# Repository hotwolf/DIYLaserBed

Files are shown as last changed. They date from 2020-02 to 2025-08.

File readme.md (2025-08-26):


# RevB
This is a DIY laser bed for K40 cutters and clones.
inside

<span></span>

---
## Table of Contents
1. [Parts list](#Parts_list)
1. [DIYLB Top Assembly](#DIYLB_top_assembly)
1. [DIYLB Carriage D Assembly](#DIYLB_carriage_D_assembly)
1. [DIYLB Carriage C Assembly](#DIYLB_carriage_C_assembly)
1. [DIYLB Carriage AB Assembly](#DIYLB_carriage_AB_assembly)
1. [DIYLB Carriage B Assembly](#DIYLB_carriage_B_assembly)
1. [DIYLB Carriage A Assembly](#DIYLB_carriage_A_assembly)
1. [DIYLB Rail Assembly](#DIYLB_rail_assembly)
1. [DIYLB Crank Assembly](#DIYLB_crank_assembly)
1. [DIYLB Idler Assembly](#DIYLB_idler_assembly)
1. [DIYLB Lower Bearing Assembly](#DIYLB_lower_bearing_assembly)
1. [DIYLB Base Right Assembly](#DIYLB_base_right_assembly)
1. [DIYLB Magnet Cover Assembly](#DIYLB_magnet_cover_assembly)
1. [DIYLB Magnet Assembly](#DIYLB_magnet_assembly)
1. [DIYLB Base Center Assembly](#DIYLB_base_center_assembly)
1. [DIYLB Base Left Assembly](#DIYLB_base_left_assembly)
1. [DIYLB Base Assembly](#DIYLB_Base_assembly)
1. [DIYLB Crank To Base Assembly](#DIYLB_crank_to_base_assembly)
1. [DIYLB Columns To Base Assembly](#DIYLB_columns_to_base_assembly)
1. [DIYLB Bed To Columns Assembly](#DIYLB_bed_to_columns_assembly)
1. [DIYLB Beams To Bed Assembly](#DIYLB_beams_to_bed_assembly)
1. [DIYLB Top To Columns Assembly](#DIYLB_top_to_columns_assembly)
1. [DIYLB Belt Assembly](#DIYLB_belt_assembly)

<span></span>
[Top](#TOP)

---

## Parts list
| <span style="writing-mode: vertical-rl; text-orientation: mixed;">2 x DIYLB&nbsp;Top</span> | <span style="writing-mode: vertical-rl; text-orientation: mixed;">DIYLB&nbsp;Carriage&nbsp;D</span> | <span style="writing-mode: vertical-rl; text-orientation: mixed;">DIYLB&nbsp;Carriage&nbsp;C</span> | <span style="writing-mode: vertical-rl; text-orientation: mixed;">2 x DIYLB&nbsp;Carriage&nbsp;AB</span> | <span style="writing-mode: vertical-rl; text-orientation: mixed;">DIYLB&nbsp;Carriage&nbsp;B</span> | <span style="writing-mode: vertical-rl; text-orientation: mixed;">DIYLB&nbsp;Carriage&nbsp;A</span> | <span style="writing-mode: vertical-rl; text-orientation: mixed;">4 x DIYLB&nbsp;Rail</span> | <span style="writing-mode: vertical-rl; text-orientation: mixed;">DIYLB&nbsp;Crank</span> | <span style="writing-mode: vertical-rl; text-orientation: mixed;">DIYLB&nbsp;Idler</span> | <span style="writing-mode: vertical-rl; text-orientation: mixed;">4 x DIYLB&nbsp;Lower&nbsp;Bearing</span> | <span style="writing-mode: vertical-rl; text-orientation: mixed;">DIYLB&nbsp;Base&nbsp;Right</span> | <span style="writing-mode: vertical-rl; text-orientation: mixed;">4 x DIYLB&nbsp;Magnet&nbsp;Cover</span> | <span style="writing-mode: vertical-rl; text-orientation: mixed;">4 x DIYLB&nbsp;Magnet</span> | <span style="writing-mode: vertical-rl; text-orientation: mixed;">2 x DIYLB&nbsp;Base&nbsp;Center</span> | <span style="writing-mode: vertical-rl; text-orientation: mixed;">DIYLB&nbsp;Base&nbsp;Left</span> | <span style="writing-mode: vertical-rl; text-orientation: mixed;">DIYLB&nbsp;Base</span> | <span style="writing-mode: vertical-rl; text-orientation: mixed;">DIYLB&nbsp;Crank&nbsp;To&nbsp;Base</span> | <span style="writing-mode: vertical-rl; text-orientation: mixed;">DIYLB&nbsp;Columns&nbsp;To&nbsp;Base</span> | <span style="writing-mode: vertical-rl; text-orientation: mixed;">DIYLB&nbsp;Bed&nbsp;To&nbsp;Columns</span> | <span style="writing-mode: vertical-rl; text-orientation: mixed;">DIYLB&nbsp;Beams&nbsp;To&nbsp;Bed</span> | <span style="writing-mode: vertical-rl; text-orientation: mixed;">DIYLB&nbsp;Top&nbsp;To&nbsp;Columns</span> | <span style="writing-mode: vertical-rl; text-orientation: mixed;">DIYLB&nbsp;Belt</span> | <span style="writing-mode: vertical-rl; text-orientation: mixed;">TOTALS</span> |  |
|---:|---:|---:|---:|---:|---:|---:|---:|---:|---:|---:|---:|---:|---:|---:|---:|---:|---:|---:|---:|---:|---:|---:|:---|
|  |  |  |  |  |  |  |  |  |  |  |  |  |  |  |  |  |  |  |  |  |  | | **Vitamins** |
| &nbsp;&nbsp;.&nbsp; | &nbsp;&nbsp;.&nbsp; | &nbsp;&nbsp;.&nbsp; | &nbsp;&nbsp;.&nbsp; | &nbsp;&nbsp;.&nbsp; | &nbsp;&nbsp;.&nbsp; | &nbsp;&nbsp;.&nbsp; | &nbsp;&nbsp;2&nbsp; | &nbsp;&nbsp;.&nbsp; | &nbsp;&nbsp;4&nbsp; | &nbsp;&nbsp;.&nbsp; | &nbsp;&nbsp;.&nbsp; | &nbsp;&nbsp;.&nbsp; | &nbsp;&nbsp;.&nbsp; | &nbsp;&nbsp;.&nbsp; | &nbsp;&nbsp;.&nbsp; | &nbsp;&nbsp;.&nbsp; | &nbsp;&nbsp;.&nbsp; | &nbsp;&nbsp;.&nbsp; | &nbsp;&nbsp;.&nbsp; | &nbsp;&nbsp;.&nbsp; | &nbsp;&nbsp;.&nbsp; |  &nbsp;&nbsp;6&nbsp; | &nbsp;&nbsp; Ball bearing 608-2RS 8mm x 22mm x 7mm |
| &nbsp;&nbsp;.&nbsp; | &nbsp;&nbsp;.&nbsp; | &nbsp;&nbsp;.&nbsp; | &nbsp;&nbsp;.&nbsp; | &nbsp;&nbsp;.&nbsp; | &nbsp;&nbsp;.&nbsp; | &nbsp;&nbsp;.&nbsp; | &nbsp;&nbsp;.&nbsp; | &nbsp;&nbsp;.&nbsp; | &nbsp;&nbsp;.&nbsp; | &nbsp;&nbsp;.&nbsp; | &nbsp;&nbsp;.&nbsp; | &nbsp;&nbsp;.&nbsp; | &nbsp;&nbsp;.&nbsp; | &nbsp;&nbsp;.&nbsp; | &nbsp;&nbsp;.&nbsp; | &nbsp;&nbsp;.&nbsp; | &nbsp;&nbsp;.&nbsp; | &nbsp;&nbsp;.&nbsp; | &nbsp;&nbsp;.&nbsp; | &nbsp;&nbsp;.&nbsp; | &nbsp;&nbsp;1&nbsp; |  &nbsp;&nbsp;1&nbsp; | &nbsp;&nbsp; Belt GT2 x 6mm x 1222mm |
| &nbsp;&nbsp;.&nbsp; | &nbsp;&nbsp;.&nbsp; | &nbsp;&nbsp;.&nbsp; | &nbsp;&nbsp;.&nbsp; | &nbsp;&nbsp;.&nbsp; | &nbsp;&nbsp;.&nbsp; | &nbsp;&nbsp;.&nbsp; | &nbsp;&nbsp;.&nbsp; | &nbsp;&nbsp;.&nbsp; | &nbsp;&nbsp;4&nbsp; | &nbsp;&nbsp;.&nbsp; | &nbsp;&nbsp;4&nbsp; | &nbsp;&nbsp;.&nbsp; | &nbsp;&nbsp;.&nbsp; | &nbsp;&nbsp;.&nbsp; | &nbsp;&nbsp;.&nbsp; | &nbsp;&nbsp;.&nbsp; | &nbsp;&nbsp;.&nbsp; | &nbsp;&nbsp;.&nbsp; | &nbsp;&nbsp;.&nbsp; | &nbsp;&nbsp;.&nbsp; | &nbsp;&nbsp;.&nbsp; |  &nbsp;&nbsp;8&nbsp; | &nbsp;&nbsp; Euro-Cent coin |
| &nbsp;&nbsp;.&nbsp; | &nbsp;&nbsp;.&nbsp; | &nbsp;&nbsp;.&nbsp; | &nbsp;&nbsp;2&nbsp; | &nbsp;&nbsp;.&nbsp; | &nbsp;&nbsp;.&nbsp; | &nbsp;&nbsp;.&nbsp; | &nbsp;&nbsp;.&nbsp; | &nbsp;&nbsp;.&nbsp; | &nbsp;&nbsp;.&nbsp; | &nbsp;&nbsp;.&nbsp; | &nbsp;&nbsp;.&nbsp; | &nbsp;&nbsp;.&nbsp; | &nbsp;&nbsp;.&nbsp; | &nbsp;&nbsp;.&nbsp; | &nbsp;&nbsp;.&nbsp; | &nbsp;&nbsp;.&nbsp; | &nbsp;&nbsp;.&nbsp; | &nbsp;&nbsp;.&nbsp; | &nbsp;&nbsp;.&nbsp; | &nbsp;&nbsp;.&nbsp; | &nbsp;&nbsp;.&nbsp; |  &nbsp;&nbsp;2&nbsp; | &nbsp;&nbsp; Extrusion E2020 x 235mm |
| &nbsp;&nbsp;.&nbsp; | &nbsp;&nbsp;.&nbsp; | &nbsp;&nbsp;.&nbsp; | &nbsp;&nbsp;.&nbsp; | &nbsp;&nbsp;.&nbsp; | &nbsp;&nbsp;.&nbsp; | &nbsp;&nbsp;.&nbsp; | &nbsp;&nbsp;.&nbsp; | &nbsp;&nbsp;.&nbsp; | &nbsp;&nbsp;.&nbsp; | &nbsp;&nbsp;1&nbsp; | &nbsp;&nbsp;.&nbsp; | &nbsp;&nbsp;.&nbsp; | &nbsp;&nbsp;.&nbsp; | &nbsp;&nbsp;1&nbsp; | &nbsp;&nbsp;.&nbsp; | &nbsp;&nbsp;.&nbsp; | &nbsp;&nbsp;.&nbsp; | &nbsp;&nbsp;.&nbsp; | &nbsp;&nbsp;.&nbsp; | &nbsp;&nbsp;.&nbsp; | &nbsp;&nbsp;.&nbsp; |  &nbsp;&nbsp;2&nbsp; | &nbsp;&nbsp; Extrusion E2020 x 300mm |
| &nbsp;&nbsp;.&nbsp; | &nbsp;&nbsp;.&nbsp; | &nbsp;&nbsp;.&nbsp; | &nbsp;&nbsp;.&nbsp; | &nbsp;&nbsp;.&nbsp; | &nbsp;&nbsp;.&nbsp; | &nbsp;&nbsp;.&nbsp; | &nbsp;&nbsp;.&nbsp; | &nbsp;&nbsp;.&nbsp; | &nbsp;&nbsp;.&nbsp; | &nbsp;&nbsp;.&nbsp; | &nbsp;&nbsp;.&nbsp; | &nbsp;&nbsp;.&nbsp; | &nbsp;&nbsp;2&nbsp; | &nbsp;&nbsp;.&nbsp; | &nbsp;&nbsp;.&nbsp; | &nbsp;&nbsp;.&nbsp; | &nbsp;&nbsp;.&nbsp; | &nbsp;&nbsp;.&nbsp; | &nbsp;&nbsp;.&nbsp; | &nbsp;&nbsp;.&nbsp; | &nbsp;&nbsp;.&nbsp; |  &nbsp;&nbsp;2&nbsp; | &nbsp;&nbsp; Extrusion E2020 x 320mm |
| &nbsp;&nbsp;.&nbsp; | &nbsp;&nbsp;.&nbsp; | &nbsp;&nbsp;.&nbsp; | &nbsp;&nbsp;.&nbsp; | &nbsp;&nbsp;.&nbsp; | &nbsp;&nbsp;.&nbsp; | &nbsp;&nbsp;4&nbsp; | &nbsp;&nbsp;.&nbsp; | &nbsp;&nbsp;.&nbsp; | &nbsp;&nbsp;.&nbsp; | &nbsp;&nbsp;.&nbsp; | &nbsp;&nbsp;.&nbsp; | &nbsp;&nbsp;.&nbsp; | &nbsp;&nbsp;.&nbsp; | &nbsp;&nbsp;.&nbsp; | &nbsp;&nbsp;.&nbsp; | &nbsp;&nbsp;.&nbsp; | &nbsp;&nbsp;.&nbsp; | &nbsp;&nbsp;.&nbsp; | &nbsp;&nbsp;.&nbsp; | &nbsp;&nbsp;.&nbsp; | &nbsp;&nbsp;.&nbsp; |  &nbsp;&nbsp;4&nbsp; | &nbsp;&nbsp; Extrusion E2020 x 70mm |
| &nbsp;&nbsp;.&nbsp; | &nbsp;&nbsp;.&nbsp; | &nbsp;&nbsp;.&nbsp; | &nbsp;&nbsp;.&nbsp; | &nbsp;&nbsp;.&nbsp; | &nbsp;&nbsp;.&nbsp; | &nbsp;&nbsp;.&nbsp; | &nbsp;&nbsp;1&nbsp; | &nbsp;&nbsp;.&nbsp; | &nbsp;&nbsp;.&nbsp; | &nbsp;&nbsp;.&nbsp; | &nbsp;&nbsp;.&nbsp; | &nbsp;&nbsp;.&nbsp; | &nbsp;&nbsp;.&nbsp; | &nbsp;&nbsp;.&nbsp; | &nbsp;&nbsp;.&nbsp; | &nbsp;&nbsp;.&nbsp; | &nbsp;&nbsp;.&nbsp; | &nbsp;&nbsp;.&nbsp; | &nbsp;&nbsp;.&nbsp; | &nbsp;&nbsp;.&nbsp; | &nbsp;&nbsp;.&nbsp; |  &nbsp;&nbsp;1&nbsp; | &nbsp;&nbsp; Extrusion E2040 x 60mm |
| &nbsp;&nbsp;.&nbsp; | &nbsp;&nbsp;.&nbsp; | &nbsp;&nbsp;.&nbsp; | &nbsp;&nbsp;.&nbsp; | &nbsp;&nbsp;.&nbsp; | &nbsp;&nbsp;.&nbsp; | &nbsp;&nbsp;.&nbsp; | &nbsp;&nbsp;1&nbsp; | &nbsp;&nbsp;.&nbsp; | &nbsp;&nbsp;.&nbsp; | &nbsp;&nbsp;.&nbsp; | &nbsp;&nbsp;.&nbsp; | &nbsp;&nbsp;.&nbsp; | &nbsp;&nbsp;.&nbsp; | &nbsp;&nbsp;.&nbsp; | &nbsp;&nbsp;.&nbsp; | &nbsp;&nbsp;.&nbsp; | &nbsp;&nbsp;.&nbsp; | &nbsp;&nbsp;.&nbsp; | &nbsp;&nbsp;.&nbsp; | &nbsp;&nbsp;.&nbsp; | &nbsp;&nbsp;.&nbsp; |  &nbsp;&nbsp;1&nbsp; | &nbsp;&nbsp; Extrusion E2040 x 70mm |
| &nbsp;&nbsp;.&nbsp; | &nbsp;&nbsp;.&nbsp; | &nbsp;&nbsp;.&nbsp; | &nbsp;&nbsp;.&nbsp; | &nbsp;&nbsp;.&nbsp; | &nbsp;&nbsp;.&nbsp; | &nbsp;&nbsp;.&nbsp; | &nbsp;&nbsp;.&nbsp; | &nbsp;&nbsp;.&nbsp; | &nbsp;&nbsp;.&nbsp; | &nbsp;&nbsp;.&nbsp; | &nbsp;&nbsp;.&nbsp; | &nbsp;&nbsp;.&nbsp; | &nbsp;&nbsp;.&nbsp; | &nbsp;&nbsp;.&nbsp; | &nbsp;&nbsp;.&nbsp; | &nbsp;&nbsp;.&nbsp; | &nbsp;&nbsp;.&nbsp; | &nbsp;&nbsp;.&nbsp; | &nbsp;&nbsp;1&nbsp; | &nbsp;&nbsp;.&nbsp; | &nbsp;&nbsp;.&nbsp; |  &nbsp;&nbsp;1&nbsp; | &nbsp;&nbsp; Flat section 15mmx2mm, 272mm |
| &nbsp;&nbsp;.&nbsp; | &nbsp;&nbsp;.&nbsp; | &nbsp;&nbsp;.&nbsp; | &nbsp;&nbsp;.&nbsp; | &nbsp;&nbsp;.&nbsp; | &nbsp;&nbsp;.&nbsp; | &nbsp;&nbsp;.&nbsp; | &nbsp;&nbsp;.&nbsp; | &nbsp;&nbsp;.&nbsp; | &nbsp;&nbsp;.&nbsp; | &nbsp;&nbsp;.&nbsp; | &nbsp;&nbsp;.&nbsp; | &nbsp;&nbsp;.&nbsp; | &nbsp;&nbsp;.&nbsp; | &nbsp;&nbsp;.&nbsp; | &nbsp;&nbsp;.&nbsp; | &nbsp;&nbsp;.&nbsp; | &nbsp;&nbsp;.&nbsp; | &nbsp;&nbsp;.&nbsp; | &nbsp;&nbsp;4&nbsp; | &nbsp;&nbsp;.&nbsp; | &nbsp;&nbsp;.&nbsp; |  &nbsp;&nbsp;4&nbsp; | &nbsp;&nbsp; Flat section 15mmx2mm, 316mm |
| &nbsp;&nbsp;.&nbsp; | &nbsp;&nbsp;.&nbsp; | &nbsp;&nbsp;.&nbsp; | &nbsp;&nbsp;.&nbsp; | &nbsp;&nbsp;.&nbsp; | &nbsp;&nbsp;.&nbsp; | &nbsp;&nbsp;.&nbsp; | &nbsp;&nbsp;2&nbsp; | &nbsp;&nbsp;.&nbsp; | &nbsp;&nbsp;.&nbsp; | &nbsp;&nbsp;2&nbsp; | &nbsp;&nbsp;.&nbsp; | &nbsp;&nbsp;.&nbsp; | &nbsp;&nbsp;.&nbsp; | &nbsp;&nbsp;4&nbsp; | &nbsp;&nbsp;.&nbsp; | &nbsp;&nbsp;.&nbsp; | &nbsp;&nbsp;.&nbsp; | &nbsp;&nbsp;.&nbsp; | &nbsp;&nbsp;.&nbsp; | &nbsp;&nbsp;.&nbsp; | &nbsp;&nbsp;.&nbsp; |  &nbsp;&nbsp;8&nbsp; | &nbsp;&nbsp; L-Bracket (20x20) |
| &nbsp;&nbsp;.&nbsp; | &nbsp;&nbsp;.&nbsp; | &nbsp;&nbsp;.&nbsp; | &nbsp;&nbsp;.&nbsp; | &nbsp;&nbsp;.&nbsp; | &nbsp;&nbsp;.&nbsp; | &nbsp;&nbsp;4&nbsp; | &nbsp;&nbsp;.&nbsp; | &nbsp;&nbsp;.&nbsp; | &nbsp;&nbsp;.&nbsp; | &nbsp;&nbsp;.&nbsp; | &nbsp;&nbsp;.&nbsp; | &nbsp;&nbsp;.&nbsp; | &nbsp;&nbsp;.&nbsp; | &nbsp;&nbsp;.&nbsp; | &nbsp;&nbsp;.&nbsp; | &nbsp;&nbsp;.&nbsp; | &nbsp;&nbsp;.&nbsp; | &nbsp;&nbsp;.&nbsp; | &nbsp;&nbsp;.&nbsp; | &nbsp;&nbsp;.&nbsp; | &nbsp;&nbsp;.&nbsp; |  &nbsp;&nbsp;4&nbsp; | &nbsp;&nbsp; Linear rail MGN7 x 70mm |
| &nbsp;&nbsp;.&nbsp; | &nbsp;&nbsp;1&nbsp; | &nbsp;&nbsp;1&nbsp; | &nbsp;&nbsp;.&nbsp; | &nbsp;&nbsp;1&nbsp; | &nbsp;&nbsp;1&nbsp; | &nbsp;&nbsp;.&nbsp; | &nbsp;&nbsp;.&nbsp; | &nbsp;&nbsp;.&nbsp; | &nbsp;&nbsp;.&nbsp; | &nbsp;&nbsp;.&nbsp; | &nbsp;&nbsp;.&nbsp; | &nbsp;&nbsp;.&nbsp; | &nbsp;&nbsp;.&nbsp; | &nbsp;&nbsp;.&nbsp; | &nbsp;&nbsp;.&nbsp; | &nbsp;&nbsp;.&nbsp; | &nbsp;&nbsp;.&nbsp; | &nbsp;&nbsp;.&nbsp; | &nbsp;&nbsp;.&nbsp; | &nbsp;&nbsp;.&nbsp; | &nbsp;&nbsp;.&nbsp; |  &nbsp;&nbsp;4&nbsp; | &nbsp;&nbsp; Linear rail carriage MGN7C |
| &nbsp;&nbsp;.&nbsp; | &nbsp;&nbsp;.&nbsp; | &nbsp;&nbsp;.&nbsp; | &nbsp;&nbsp;.&nbsp; | &nbsp;&nbsp;.&nbsp; | &nbsp;&nbsp;.&nbsp; | &nbsp;&nbsp;.&nbsp; | &nbsp;&nbsp;.&nbsp; | &nbsp;&nbsp;.&nbsp; | &nbsp;&nbsp;.&nbsp; | &nbsp;&nbsp;.&nbsp; | &nbsp;&nbsp;.&nbsp; | &nbsp;&nbsp;4&nbsp; | &nbsp;&nbsp;.&nbsp; | &nbsp;&nbsp;.&nbsp; | &nbsp;&nbsp;.&nbsp; | &nbsp;&nbsp;.&nbsp; | &nbsp;&nbsp;.&nbsp; | &nbsp;&nbsp;.&nbsp; | &nbsp;&nbsp;.&nbsp; | &nbsp;&nbsp;.&nbsp; | &nbsp;&nbsp;.&nbsp; |  &nbsp;&nbsp;4&nbsp; | &nbsp;&nbsp; Neodym Magnet (D=20,H=4.5) |
| &nbsp;&nbsp;.&nbsp; | &nbsp;&nbsp;.&nbsp; | &nbsp;&nbsp;.&nbsp; | &nbsp;&nbsp;.&nbsp; | &nbsp;&nbsp;.&nbsp; | &nbsp;&nbsp;.&nbsp; | &nbsp;&nbsp;20&nbsp; | &nbsp;&nbsp;.&nbsp; | &nbsp;&nbsp;.&nbsp; | &nbsp;&nbsp;.&nbsp; | &nbsp;&nbsp;.&nbsp; | &nbsp;&nbsp;.&nbsp; | &nbsp;&nbsp;.&nbsp; | &nbsp;&nbsp;.&nbsp; | &nbsp;&nbsp;.&nbsp; | &nbsp;&nbsp;.&nbsp; | &nbsp;&nbsp;.&nbsp; | &nbsp;&nbsp;.&nbsp; | &nbsp;&nbsp;.&nbsp; | &nbsp;&nbsp;.&nbsp; | &nbsp;&nbsp;.&nbsp; | &nbsp;&nbsp;.&nbsp; |  &nbsp;&nbsp;20&nbsp; | &nbsp;&nbsp; Nut M2 x 1.6mm  |
| &nbsp;&nbsp;.&nbsp; | &nbsp;&nbsp;2&nbsp; | &nbsp;&nbsp;2&nbsp; | &nbsp;&nbsp;.&nbsp; | &nbsp;&nbsp;2&nbsp; | &nbsp;&nbsp;2&nbsp; | &nbsp;&nbsp;.&nbsp; | &nbsp;&nbsp;.&nbsp; | &nbsp;&nbsp;.&nbsp; | &nbsp;&nbsp;.&nbsp; | &nbsp;&nbsp;.&nbsp; | &nbsp;&nbsp;.&nbsp; | &nbsp;&nbsp;.&nbsp; | &nbsp;&nbsp;.&nbsp; | &nbsp;&nbsp;.&nbsp; | &nbsp;&nbsp;.&nbsp; | &nbsp;&nbsp;.&nbsp; | &nbsp;&nbsp;.&nbsp; | &nbsp;&nbsp;.&nbsp; | &nbsp;&nbsp;.&nbsp; | &nbsp;&nbsp;.&nbsp; | &nbsp;&nbsp;.&nbsp; |  &nbsp;&nbsp;8&nbsp; | &nbsp;&nbsp; Nut M3 x 2.4mm  |
| &nbsp;&nbsp;.&nbsp; | &nbsp;&nbsp;.&nbsp; | &nbsp;&nbsp;.&nbsp; | &nbsp;&nbsp;.&nbsp; | &nbsp;&nbsp;.&nbsp; | &nbsp;&nbsp;.&nbsp; | &nbsp;&nbsp;.&nbsp; | &nbsp;&nbsp;.&nbsp; | &nbsp;&nbsp;1&nbsp; | &nbsp;&nbsp;.&nbsp; | &nbsp;&nbsp;.&nbsp; | &nbsp;&nbsp;.&nbsp; | &nbsp;&nbsp;.&nbsp; | &nbsp;&nbsp;.&nbsp; | &nbsp;&nbsp;.&nbsp; | &nbsp;&nbsp;.&nbsp; | &nbsp;&nbsp;.&nbsp; | &nbsp;&nbsp;.&nbsp; | &nbsp;&nbsp;.&nbsp; | &nbsp;&nbsp;.&nbsp; | &nbsp;&nbsp;.&nbsp; | &nbsp;&nbsp;.&nbsp; |  &nbsp;&nbsp;1&nbsp; | &nbsp;&nbsp; Nut M5 x 4mm  |
| &nbsp;&nbsp;.&nbsp; | &nbsp;&nbsp;.&nbsp; | &nbsp;&nbsp;.&nbsp; | &nbsp;&nbsp;.&nbsp; | &nbsp;&nbsp;.&nbsp; | &nbsp;&nbsp;.&nbsp; | &nbsp;&nbsp;.&nbsp; | &nbsp;&nbsp;1&nbsp; | &nbsp;&nbsp;.&nbsp; | &nbsp;&nbsp;.&nbsp; | &nbsp;&nbsp;.&nbsp; | &nbsp;&nbsp;.&nbsp; | &nbsp;&nbsp;.&nbsp; | &nbsp;&nbsp;.&nbsp; | &nbsp;&nbsp;.&nbsp; | &nbsp;&nbsp;.&nbsp; | &nbsp;&nbsp;.&nbsp; | &nbsp;&nbsp;.&nbsp; | &nbsp;&nbsp;.&nbsp; | &nbsp;&nbsp;.&nbsp; | &nbsp;&nbsp;.&nbsp; | &nbsp;&nbsp;.&nbsp; |  &nbsp;&nbsp;1&nbsp; | &nbsp;&nbsp; Nut M8 x 6.5mm  |
| &nbsp;&nbsp;.&nbsp; | &nbsp;&nbsp;.&nbsp; | &nbsp;&nbsp;.&nbsp; | &nbsp;&nbsp;.&nbsp; | &nbsp;&nbsp;.&nbsp; | &nbsp;&nbsp;.&nbsp; | &nbsp;&nbsp;.&nbsp; | &nbsp;&nbsp;.&nbsp; | &nbsp;&nbsp;1&nbsp; | &nbsp;&nbsp;.&nbsp; | &nbsp;&nbsp;.&nbsp; | &nbsp;&nbsp;.&nbsp; | &nbsp;&nbsp;.&nbsp; | &nbsp;&nbsp;.&nbsp; | &nbsp;&nbsp;.&nbsp; | &nbsp;&nbsp;.&nbsp; | &nbsp;&nbsp;.&nbsp; | &nbsp;&nbsp;.&nbsp; | &nbsp;&nbsp;.&nbsp; | &nbsp;&nbsp;.&nbsp; | &nbsp;&nbsp;.&nbsp; | &nbsp;&nbsp;.&nbsp; |  &nbsp;&nbsp;1&nbsp; | &nbsp;&nbsp; Pulley GT2 idler 20 teeth |
| &nbsp;&nbsp;.&nbsp; | &nbsp;&nbsp;.&nbsp; | &nbsp;&nbsp;.&nbsp; | &nbsp;&nbsp;.&nbsp; | &nbsp;&nbsp;.&nbsp; | &nbsp;&nbsp;.&nbsp; | &nbsp;&nbsp;.&nbsp; | &nbsp;&nbsp;2&nbsp; | &nbsp;&nbsp;.&nbsp; | &nbsp;&nbsp;.&nbsp; | &nbsp;&nbsp;.&nbsp; | &nbsp;&nbsp;.&nbsp; | &nbsp;&nbsp;.&nbsp; | &nbsp;&nbsp;.&nbsp; | &nbsp;&nbsp;.&nbsp; | &nbsp;&nbsp;.&nbsp; | &nbsp;&nbsp;.&nbsp; | &nbsp;&nbsp;.&nbsp; | &nbsp;&nbsp;.&nbsp; | &nbsp;&nbsp;.&nbsp; | &nbsp;&nbsp;.&nbsp; | &nbsp;&nbsp;.&nbsp; |  &nbsp;&nbsp;2&nbsp; | &nbsp;&nbsp; Pulley GT2 idler smooth 12mm |
| &nbsp;&nbsp;.&nbsp; | &nbsp;&nbsp;.&nbsp; | &nbsp;&nbsp;.&nbsp; | &nbsp;&nbsp;.&nbsp; | &nbsp;&nbsp;.&nbsp; | &nbsp;&nbsp;.&nbsp; | &nbsp;&nbsp;.&nbsp; | &nbsp;&nbsp;1&nbsp; | &nbsp;&nbsp;.&nbsp; | &nbsp;&nbsp;4&nbsp; | &nbsp;&nbsp;.&nbsp; | &nbsp;&nbsp;.&nbsp; | &nbsp;&nbsp;.&nbsp; | &nbsp;&nbsp;.&nbsp; | &nbsp;&nbsp;.&nbsp; | &nbsp;&nbsp;.&nbsp; | &nbsp;&nbsp;.&nbsp; | &nbsp;&nbsp;.&nbsp; | &nbsp;&nbsp;.&nbsp; | &nbsp;&nbsp;.&nbsp; | &nbsp;&nbsp;.&nbsp; | &nbsp;&nbsp;.&nbsp; |  &nbsp;&nbsp;5&nbsp; | &nbsp;&nbsp; Pulley GT2OB 20 teeth |
| &nbsp;&nbsp;.&nbsp; | &nbsp;&nbsp;.&nbsp; | &nbsp;&nbsp;.&nbsp; | &nbsp;&nbsp;.&nbsp; | &nbsp;&nbsp;.&nbsp; | &nbsp;&nbsp;.&nbsp; | &nbsp;&nbsp;20&nbsp; | &nbsp;&nbsp;.&nbsp; | &nbsp;&nbsp;.&nbsp; | &nbsp;&nbsp;.&nbsp; | &nbsp;&nbsp;.&nbsp; | &nbsp;&nbsp;.&nbsp; | &nbsp;&nbsp;.&nbsp; | &nbsp;&nbsp;.&nbsp; | &nbsp;&nbsp;.&nbsp; | &nbsp;&nbsp;.&nbsp; | &nbsp;&nbsp;.&nbsp; | &nbsp;&nbsp;.&nbsp; | &nbsp;&nbsp;.&nbsp; | &nbsp;&nbsp;.&nbsp; | &nbsp;&nbsp;.&nbsp; | &nbsp;&nbsp;.&nbsp; |  &nbsp;&nbsp;20&nbsp; | &nbsp;&nbsp; Screw M2 cap x  6mm |
| &nbsp;&nbsp;.&nbsp; | &nbsp;&nbsp;4&nbsp; | &nbsp;&nbsp;4&nbsp; | &nbsp;&nbsp;.&nbsp; | &nbsp;&nbsp;4&nbsp; | &nbsp;&nbsp;4&nbsp; | &nbsp;&nbsp;.&nbsp; | &nbsp;&nbsp;.&nbsp; | &nbsp;&nbsp;.&nbsp; | &nbsp;&nbsp;.&nbsp; | &nbsp;&nbsp;.&nbsp; | &nbsp;&nbsp;.&nbsp; | &nbsp;&nbsp;.&nbsp; | &nbsp;&nbsp;.&nbsp; | &nbsp;&nbsp;.&nbsp; | &nbsp;&nbsp;.&nbsp; | &nbsp;&nbsp;.&nbsp; | &nbsp;&nbsp;.&nbsp; | &nbsp;&nbsp;.&nbsp; | &nbsp;&nbsp;.&nbsp; | &nbsp;&nbsp;.&nbsp; | &nbsp;&nbsp;.&nbsp; |  &nbsp;&nbsp;16&nbsp; | &nbsp;&nbsp; Screw M2 cap x 10mm |
| &nbsp;&nbsp;.&nbsp; | &nbsp;&nbsp;.&nbsp; | &nbsp;&nbsp;.&nbsp; | &nbsp;&nbsp;.&nbsp; | &nbsp;&nbsp;.&nbsp; | &nbsp;&nbsp;.&nbsp; | &nbsp;&nbsp;.&nbsp; | &nbsp;&nbsp;6&nbsp; | &nbsp;&nbsp;.&nbsp; | &nbsp;&nbsp;8&nbsp; | &nbsp;&nbsp;4&nbsp; | &nbsp;&nbsp;.&nbsp; | &nbsp;&nbsp;.&nbsp; | &nbsp;&nbsp;.&nbsp; | &nbsp;&nbsp;8&nbsp; | &nbsp;&nbsp;.&nbsp; | &nbsp;&nbsp;.&nbsp; | &nbsp;&nbsp;.&nbsp; | &nbsp;&nbsp;.&nbsp; | &nbsp;&nbsp;.&nbsp; | &nbsp;&nbsp;.&nbsp; | &nbsp;&nbsp;.&nbsp; |  &nbsp;&nbsp;26&nbsp; | &nbsp;&nbsp; Screw M3 grub x  6mm |
| &nbsp;&nbsp;.&nbsp; | &nbsp;&nbsp;2&nbsp; | &nbsp;&nbsp;2&nbsp; | &nbsp;&nbsp;.&nbsp; | &nbsp;&nbsp;2&nbsp; | &nbsp;&nbsp;2&nbsp; | &nbsp;&nbsp;.&nbsp; | &nbsp;&nbsp;.&nbsp; | &nbsp;&nbsp;.&nbsp; | &nbsp;&nbsp;.&nbsp; | &nbsp;&nbsp;.&nbsp; | &nbsp;&nbsp;.&nbsp; | &nbsp;&nbsp;.&nbsp; | &nbsp;&nbsp;.&nbsp; | &nbsp;&nbsp;.&nbsp; | &nbsp;&nbsp;.&nbsp; | &nbsp;&nbsp;.&nbsp; | &nbsp;&nbsp;.&nbsp; | &nbsp;&nbsp;.&nbsp; | &nbsp;&nbsp;.&nbsp; | &nbsp;&nbsp;.&nbsp; | &nbsp;&nbsp;.&nbsp; |  &nbsp;&nbsp;8&nbsp; | &nbsp;&nbsp; Screw M3 pan x 12mm |
| &nbsp;&nbsp;.&nbsp; | &nbsp;&nbsp;1&nbsp; | &nbsp;&nbsp;1&nbsp; | &nbsp;&nbsp;.&nbsp; | &nbsp;&nbsp;1&nbsp; | &nbsp;&nbsp;1&nbsp; | &nbsp;&nbsp;.&nbsp; | &nbsp;&nbsp;.&nbsp; | &nbsp;&nbsp;2&nbsp; | &nbsp;&nbsp;8&nbsp; | &nbsp;&nbsp;.&nbsp; | &nbsp;&nbsp;.&nbsp; | &nbsp;&nbsp;8&nbsp; | &nbsp;&nbsp;.&nbsp; | &nbsp;&nbsp;.&nbsp; | &nbsp;&nbsp;.&nbsp; | &nbsp;&nbsp;.&nbsp; | &nbsp;&nbsp;.&nbsp; | &nbsp;&nbsp;.&nbsp; | &nbsp;&nbsp;.&nbsp; | &nbsp;&nbsp;.&nbsp; | &nbsp;&nbsp;.&nbsp; |  &nbsp;&nbsp;22&nbsp; | &nbsp;&nbsp; Screw M4 cap x 12mm |
| &nbsp;&nbsp;.&nbsp; | &nbsp;&nbsp;.&nbsp; | &nbsp;&nbsp;.&nbsp; | &nbsp;&nbsp;.&nbsp; | &nbsp;&nbsp;.&nbsp; | &nbsp;&nbsp;.&nbsp; | &nbsp;&nbsp;.&nbsp; | &nbsp;&nbsp;2&nbsp; | &nbsp;&nbsp;.&nbsp; | &nbsp;&nbsp;.&nbsp; | &nbsp;&nbsp;.&nbsp; | &nbsp;&nbsp;.&nbsp; | &nbsp;&nbsp;.&nbsp; | &nbsp;&nbsp;.&nbsp; | &nbsp;&nbsp;.&nbsp; | &nbsp;&nbsp;.&nbsp; | &nbsp;&nbsp;.&nbsp; | &nbsp;&nbsp;.&nbsp; | &nbsp;&nbsp;.&nbsp; | &nbsp;&nbsp;.&nbsp; | &nbsp;&nbsp;.&nbsp; | &nbsp;&nbsp;.&nbsp; |  &nbsp;&nbsp;2&nbsp; | &nbsp;&nbsp; Screw M4 cap x 15mm |
| &nbsp;&nbsp;.&nbsp; | &nbsp;&nbsp;.&nbsp; | &nbsp;&nbsp;.&nbsp; | &nbsp;&nbsp;.&nbsp; | &nbsp;&nbsp;.&nbsp; | &nbsp;&nbsp;.&nbsp; | &nbsp;&nbsp;.&nbsp; | &nbsp;&nbsp;4&nbsp; | &nbsp;&nbsp;.&nbsp; | &nbsp;&nbsp;.&nbsp; | &nbsp;&nbsp;.&nbsp; | &nbsp;&nbsp;.&nbsp; | &nbsp;&nbsp;.&nbsp; | &nbsp;&nbsp;.&nbsp; | &nbsp;&nbsp;.&nbsp; | &nbsp;&nbsp;.&nbsp; | &nbsp;&nbsp;.&nbsp; | &nbsp;&nbsp;.&nbsp; | &nbsp;&nbsp;.&nbsp; | &nbsp;&nbsp;.&nbsp; | &nbsp;&nbsp;.&nbsp; | &nbsp;&nbsp;.&nbsp; |  &nbsp;&nbsp;4&nbsp; | &nbsp;&nbsp; Screw M4 dome x  8mm |
| &nbsp;&nbsp;.&nbsp; | &nbsp;&nbsp;.&nbsp; | &nbsp;&nbsp;.&nbsp; | &nbsp;&nbsp;.&nbsp; | &nbsp;&nbsp;.&nbsp; | &nbsp;&nbsp;.&nbsp; | &nbsp;&nbsp;.&nbsp; | &nbsp;&nbsp;.&nbsp; | &nbsp;&nbsp;1&nbsp; | &nbsp;&nbsp;.&nbsp; | &nbsp;&nbsp;.&nbsp; | &nbsp;&nbsp;.&nbsp; | &nbsp;&nbsp;.&nbsp; | &nbsp;&nbsp;.&nbsp; | &nbsp;&nbsp;.&nbsp; | &nbsp;&nbsp;.&nbsp; | &nbsp;&nbsp;.&nbsp; | &nbsp;&nbsp;.&nbsp; | &nbsp;&nbsp;.&nbsp; | &nbsp;&nbsp;.&nbsp; | &nbsp;&nbsp;.&nbsp; | &nbsp;&nbsp;.&nbsp; |  &nbsp;&nbsp;1&nbsp; | &nbsp;&nbsp; Screw M5 cap x 28mm |
| &nbsp;&nbsp;4&nbsp; | &nbsp;&nbsp;.&nbsp; | &nbsp;&nbsp;.&nbsp; | &nbsp;&nbsp;.&nbsp; | &nbsp;&nbsp;.&nbsp; | &nbsp;&nbsp;.&nbsp; | &nbsp;&nbsp;.&nbsp; | &nbsp;&nbsp;.&nbsp; | &nbsp;&nbsp;.&nbsp; | &nbsp;&nbsp;.&nbsp; | &nbsp;&nbsp;.&nbsp; | &nbsp;&nbsp;.&nbsp; | &nbsp;&nbsp;.&nbsp; | &nbsp;&nbsp;.&nbsp; | &nbsp;&nbsp;.&nbsp; | &nbsp;&nbsp;.&nbsp; | &nbsp;&nbsp;.&nbsp; | &nbsp;&nbsp;.&nbsp; | &nbsp;&nbsp;.&nbsp; | &nbsp;&nbsp;.&nbsp; | &nbsp;&nbsp;.&nbsp; | &nbsp;&nbsp;.&nbsp; |  &nbsp;&nbsp;4&nbsp; | &nbsp;&nbsp; Screw M6 cap x 20mm |
| &nbsp;&nbsp;.&nbsp; | &nbsp;&nbsp;1&nbsp; | &nbsp;&nbsp;1&nbsp; | &nbsp;&nbsp;.&nbsp; | &nbsp;&nbsp;1&nbsp; | &nbsp;&nbsp;1&nbsp; | &nbsp;&nbsp;.&nbsp; | &nbsp;&nbsp;.&nbsp; | &nbsp;&nbsp;.&nbsp; | &nbsp;&nbsp;.&nbsp; | &nbsp;&nbsp;.&nbsp; | &nbsp;&nbsp;.&nbsp; | &nbsp;&nbsp;.&nbsp; | &nbsp;&nbsp;.&nbsp; | &nbsp;&nbsp;.&nbsp; | &nbsp;&nbsp;.&nbsp; | &nbsp;&nbsp;.&nbsp; | &nbsp;&nbsp;.&nbsp; | &nbsp;&nbsp;.&nbsp; | &nbsp;&nbsp;.&nbsp; | &nbsp;&nbsp;.&nbsp; | &nbsp;&nbsp;.&nbsp; |  &nbsp;&nbsp;4&nbsp; | &nbsp;&nbsp; Screw M6 pan x 20mm |
| &nbsp;&nbsp;.&nbsp; | &nbsp;&nbsp;.&nbsp; | &nbsp;&nbsp;.&nbsp; | &nbsp;&nbsp;.&nbsp; | &nbsp;&nbsp;.&nbsp; | &nbsp;&nbsp;.&nbsp; | &nbsp;&nbsp;.&nbsp; | &nbsp;&nbsp;3&nbsp; | &nbsp;&nbsp;.&nbsp; | &nbsp;&nbsp;.&nbsp; | &nbsp;&nbsp;.&nbsp; | &nbsp;&nbsp;.&nbsp; | &nbsp;&nbsp;.&nbsp; | &nbsp;&nbsp;.&nbsp; | &nbsp;&nbsp;.&nbsp; | &nbsp;&nbsp;.&nbsp; | &nbsp;&nbsp;.&nbsp; | &nbsp;&nbsp;.&nbsp; | &nbsp;&nbsp;.&nbsp; | &nbsp;&nbsp;.&nbsp; | &nbsp;&nbsp;.&nbsp; | &nbsp;&nbsp;.&nbsp; |  &nbsp;&nbsp;3&nbsp; | &nbsp;&nbsp; Screw M8 hex x 50mm |
| &nbsp;&nbsp;.&nbsp; | &nbsp;&nbsp;1&nbsp; | &nbsp;&nbsp;1&nbsp; | &nbsp;&nbsp;.&nbsp; | &nbsp;&nbsp;1&nbsp; | &nbsp;&nbsp;1&nbsp; | &nbsp;&nbsp;.&nbsp; | &nbsp;&nbsp;.&nbsp; | &nbsp;&nbsp;2&nbsp; | &nbsp;&nbsp;8&nbsp; | &nbsp;&nbsp;.&nbsp; | &nbsp;&nbsp;.&nbsp; | &nbsp;&nbsp;8&nbsp; | &nbsp;&nbsp;.&nbsp; | &nbsp;&nbsp;.&nbsp; | &nbsp;&nbsp;.&nbsp; | &nbsp;&nbsp;.&nbsp; | &nbsp;&nbsp;.&nbsp; | &nbsp;&nbsp;.&nbsp; | &nbsp;&nbsp;.&nbsp; | &nbsp;&nbsp;.&nbsp; | &nbsp;&nbsp;.&nbsp; |  &nbsp;&nbsp;22&nbsp; | &nbsp;&nbsp; T-Nut (20x20) |
| &nbsp;&nbsp;.&nbsp; | &nbsp;&nbsp;.&nbsp; | &nbsp;&nbsp;.&nbsp; | &nbsp;&nbsp;.&nbsp; | &nbsp;&nbsp;.&nbsp; | &nbsp;&nbsp;.&nbsp; | &nbsp;&nbsp;.&nbsp; | &nbsp;&nbsp;4&nbsp; | &nbsp;&nbsp;.&nbsp; | &nbsp;&nbsp;.&nbsp; | &nbsp;&nbsp;.&nbsp; | &nbsp;&nbsp;.&nbsp; | &nbsp;&nbsp;.&nbsp; | &nbsp;&nbsp;.&nbsp; | &nbsp;&nbsp;.&nbsp; | &nbsp;&nbsp;.&nbsp; | &nbsp;&nbsp;.&nbsp; | &nbsp;&nbsp;.&nbsp; | &nbsp;&nbsp;.&nbsp; | &nbsp;&nbsp;.&nbsp; | &nbsp;&nbsp;.&nbsp; | &nbsp;&nbsp;.&nbsp; |  &nbsp;&nbsp;4&nbsp; | &nbsp;&nbsp; T-Nut (20x20) |
| &nbsp;&nbsp;.&nbsp; | &nbsp;&nbsp;.&nbsp; | &nbsp;&nbsp;.&nbsp; | &nbsp;&nbsp;.&nbsp; | &nbsp;&nbsp;.&nbsp; | &nbsp;&nbsp;.&nbsp; | &nbsp;&nbsp;.&nbsp; | &nbsp;&nbsp;2&nbsp; | &nbsp;&nbsp;.&nbsp; | &nbsp;&nbsp;.&nbsp; | &nbsp;&nbsp;.&nbsp; | &nbsp;&nbsp;.&nbsp; | &nbsp;&nbsp;.&nbsp; | &nbsp;&nbsp;.&nbsp; | &nbsp;&nbsp;.&nbsp; | &nbsp;&nbsp;.&nbsp; | &nbsp;&nbsp;.&nbsp; | &nbsp;&nbsp;.&nbsp; | &nbsp;&nbsp;.&nbsp; | &nbsp;&nbsp;.&nbsp; | &nbsp;&nbsp;.&nbsp; | &nbsp;&nbsp;.&nbsp; |  &nbsp;&nbsp;2&nbsp; | &nbsp;&nbsp; T-Nut (20x20) |
| &nbsp;&nbsp;.&nbsp; | &nbsp;&nbsp;1&nbsp; | &nbsp;&nbsp;1&nbsp; | &nbsp;&nbsp;.&nbsp; | &nbsp;&nbsp;1&nbsp; | &nbsp;&nbsp;1&nbsp; | &nbsp;&nbsp;.&nbsp; | &nbsp;&nbsp;.&nbsp; | &nbsp;&nbsp;.&nbsp; | &nbsp;&nbsp;.&nbsp; | &nbsp;&nbsp;.&nbsp; | &nbsp;&nbsp;.&nbsp; | &nbsp;&nbsp;.&nbsp; | &nbsp;&nbsp;.&nbsp; | &nbsp;&nbsp;.&nbsp; | &nbsp;&nbsp;.&nbsp; | &nbsp;&nbsp;.&nbsp; | &nbsp;&nbsp;.&nbsp; | &nbsp;&nbsp;.&nbsp; | &nbsp;&nbsp;.&nbsp; | &nbsp;&nbsp;.&nbsp; | &nbsp;&nbsp;.&nbsp; |  &nbsp;&nbsp;4&nbsp; | &nbsp;&nbsp; T8-Nut (narrow) |
| &nbsp;&nbsp;.&nbsp; | &nbsp;&nbsp;.&nbsp; | &nbsp;&nbsp;.&nbsp; | &nbsp;&nbsp;.&nbsp; | &nbsp;&nbsp;.&nbsp; | &nbsp;&nbsp;.&nbsp; | &nbsp;&nbsp;.&nbsp; | &nbsp;&nbsp;.&nbsp; | &nbsp;&nbsp;.&nbsp; | &nbsp;&nbsp;4&nbsp; | &nbsp;&nbsp;.&nbsp; | &nbsp;&nbsp;.&nbsp; | &nbsp;&nbsp;.&nbsp; | &nbsp;&nbsp;.&nbsp; | &nbsp;&nbsp;.&nbsp; | &nbsp;&nbsp;.&nbsp; | &nbsp;&nbsp;.&nbsp; | &nbsp;&nbsp;.&nbsp; | &nbsp;&nbsp;.&nbsp; | &nbsp;&nbsp;.&nbsp; | &nbsp;&nbsp;.&nbsp; | &nbsp;&nbsp;.&nbsp; |  &nbsp;&nbsp;4&nbsp; | &nbsp;&nbsp; Threaded rod M8 x 100mm |
| &nbsp;&nbsp;.&nbsp; | &nbsp;&nbsp;4&nbsp; | &nbsp;&nbsp;4&nbsp; | &nbsp;&nbsp;.&nbsp; | &nbsp;&nbsp;4&nbsp; | &nbsp;&nbsp;4&nbsp; | &nbsp;&nbsp;.&nbsp; | &nbsp;&nbsp;.&nbsp; | &nbsp;&nbsp;.&nbsp; | &nbsp;&nbsp;.&nbsp; | &nbsp;&nbsp;.&nbsp; | &nbsp;&nbsp;.&nbsp; | &nbsp;&nbsp;.&nbsp; | &nbsp;&nbsp;.&nbsp; | &nbsp;&nbsp;.&nbsp; | &nbsp;&nbsp;.&nbsp; | &nbsp;&nbsp;.&nbsp; | &nbsp;&nbsp;.&nbsp; | &nbsp;&nbsp;.&nbsp; | &nbsp;&nbsp;.&nbsp; | &nbsp;&nbsp;.&nbsp; | &nbsp;&nbsp;.&nbsp; |  &nbsp;&nbsp;16&nbsp; | &nbsp;&nbsp; Washer  M2 x 5mm x 0.3mm |
| &nbsp;&nbsp;.&nbsp; | &nbsp;&nbsp;1&nbsp; | &nbsp;&nbsp;1&nbsp; | &nbsp;&nbsp;.&nbsp; | &nbsp;&nbsp;1&nbsp; | &nbsp;&nbsp;1&nbsp; | &nbsp;&nbsp;.&nbsp; | &nbsp;&nbsp;6&nbsp; | &nbsp;&nbsp;2&nbsp; | &nbsp;&nbsp;8&nbsp; | &nbsp;&nbsp;.&nbsp; | &nbsp;&nbsp;.&nbsp; | &nbsp;&nbsp;8&nbsp; | &nbsp;&nbsp;.&nbsp; | &nbsp;&nbsp;.&nbsp; | &nbsp;&nbsp;.&nbsp; | &nbsp;&nbsp;.&nbsp; | &nbsp;&nbsp;.&nbsp; | &nbsp;&nbsp;.&nbsp; | &nbsp;&nbsp;.&nbsp; | &nbsp;&nbsp;.&nbsp; | &nbsp;&nbsp;.&nbsp; |  &nbsp;&nbsp;28&nbsp; | &nbsp;&nbsp; Washer  M4 x 9mm x 0.8mm |
| &nbsp;&nbsp;.&nbsp; | &nbsp;&nbsp;.&nbsp; | &nbsp;&nbsp;.&nbsp; | &nbsp;&nbsp;.&nbsp; | &nbsp;&nbsp;.&nbsp; | &nbsp;&nbsp;.&nbsp; | &nbsp;&nbsp;.&nbsp; | &nbsp;&nbsp;.&nbsp; | &nbsp;&nbsp;1&nbsp; | &nbsp;&nbsp;.&nbsp; | &nbsp;&nbsp;.&nbsp; | &nbsp;&nbsp;.&nbsp; | &nbsp;&nbsp;.&nbsp; | &nbsp;&nbsp;.&nbsp; | &nbsp;&nbsp;.&nbsp; | &nbsp;&nbsp;.&nbsp; | &nbsp;&nbsp;.&nbsp; | &nbsp;&nbsp;.&nbsp; | &nbsp;&nbsp;.&nbsp; | &nbsp;&nbsp;.&nbsp; | &nbsp;&nbsp;.&nbsp; | &nbsp;&nbsp;.&nbsp; |  &nbsp;&nbsp;1&nbsp; | &nbsp;&nbsp; Washer  M5 x 10mm x 1mm |
| &nbsp;&nbsp;4&nbsp; | &nbsp;&nbsp;1&nbsp; | &nbsp;&nbsp;1&nbsp; | &nbsp;&nbsp;.&nbsp; | &nbsp;&nbsp;1&nbsp; | &nbsp;&nbsp;1&nbsp; | &nbsp;&nbsp;.&nbsp; | &nbsp;&nbsp;.&nbsp; | &nbsp;&nbsp;.&nbsp; | &nbsp;&nbsp;.&nbsp; | &nbsp;&nbsp;.&nbsp; | &nbsp;&nbsp;.&nbsp; | &nbsp;&nbsp;.&nbsp; | &nbsp;&nbsp;.&nbsp; | &nbsp;&nbsp;.&nbsp; | &nbsp;&nbsp;.&nbsp; | &nbsp;&nbsp;.&nbsp; | &nbsp;&nbsp;.&nbsp; | &nbsp;&nbsp;.&nbsp; | &nbsp;&nbsp;.&nbsp; | &nbsp;&nbsp;.&nbsp; | &nbsp;&nbsp;.&nbsp; |  &nbsp;&nbsp;8&nbsp; | &nbsp;&nbsp; Washer  M6 x 12.5mm x 1.5mm |
| &nbsp;&nbsp;8&nbsp; | &nbsp;&nbsp;19&nbsp; | &nbsp;&nbsp;19&nbsp; | &nbsp;&nbsp;2&nbsp; | &nbsp;&nbsp;19&nbsp; | &nbsp;&nbsp;19&nbsp; | &nbsp;&nbsp;48&nbsp; | &nbsp;&nbsp;37&nbsp; | &nbsp;&nbsp;10&nbsp; | &nbsp;&nbsp;48&nbsp; | &nbsp;&nbsp;7&nbsp; | &nbsp;&nbsp;4&nbsp; | &nbsp;&nbsp;28&nbsp; | &nbsp;&nbsp;2&nbsp; | &nbsp;&nbsp;13&nbsp; | &nbsp;&nbsp;.&nbsp; | &nbsp;&nbsp;.&nbsp; | &nbsp;&nbsp;.&nbsp; | &nbsp;&nbsp;.&nbsp; | &nbsp;&nbsp;5&nbsp; | &nbsp;&nbsp;.&nbsp; | &nbsp;&nbsp;1&nbsp; | &nbsp;&nbsp;289&nbsp; | &nbsp;&nbsp;Total vitamins count |
|  |  |  |  |  |  |  |  |  |  |  |  |  |  |  |  |  |  |  |  |  |  | | **3D printed parts** |
| &nbsp;&nbsp;.&nbsp; | &nbsp;&nbsp;.&nbsp; | &nbsp;&nbsp;.&nbsp; | &nbsp;&nbsp;.&nbsp; | &nbsp;&nbsp;.&nbsp; | &nbsp;&nbsp;.&nbsp; | &nbsp;&nbsp;.&nbsp; | &nbsp;&nbsp;.&nbsp; | &nbsp;&nbsp;.&nbsp; | &nbsp;&nbsp;.&nbsp; | &nbsp;&nbsp;.&nbsp; | &nbsp;&nbsp;.&nbsp; | &nbsp;&nbsp;.&nbsp; | &nbsp;&nbsp;.&nbsp; | &nbsp;&nbsp;.&nbsp; | &nbsp;&nbsp;.&nbsp; | &nbsp;&nbsp;.&nbsp; | &nbsp;&nbsp;.&nbsp; | &nbsp;&nbsp;.&nbsp; | &nbsp;&nbsp;8&nbsp; | &nbsp;&nbsp;.&nbsp; | &nbsp;&nbsp;.&nbsp; |  &nbsp;&nbsp;8&nbsp; | &nbsp;&nbsp;DIYLB_beam_holder.stl |
| &nbsp;&nbsp;.&nbsp; | &nbsp;&nbsp;.&nbsp; | &nbsp;&nbsp;.&nbsp; | &nbsp;&nbsp;.&nbsp; | &nbsp;&nbsp;.&nbsp; | &nbsp;&nbsp;1&nbsp; | &nbsp;&nbsp;.&nbsp; | &nbsp;&nbsp;.&nbsp; | &nbsp;&nbsp;.&nbsp; | &nbsp;&nbsp;.&nbsp; | &nbsp;&nbsp;.&nbsp; | &nbsp;&nbsp;.&nbsp; | &nbsp;&nbsp;.&nbsp; | &nbsp;&nbsp;.&nbsp; | &nbsp;&nbsp;.&nbsp; | &nbsp;&nbsp;.&nbsp; | &nbsp;&nbsp;.&nbsp; | &nbsp;&nbsp;.&nbsp; | &nbsp;&nbsp;.&nbsp; | &nbsp;&nbsp;.&nbsp; | &nbsp;&nbsp;.&nbsp; | &nbsp;&nbsp;.&nbsp; |  &nbsp;&nbsp;1&nbsp; | &nbsp;&nbsp;DIYLB_carriage_A.stl |
| &nbsp;&nbsp;.&nbsp; | &nbsp;&nbsp;.&nbsp; | &nbsp;&nbsp;.&nbsp; | &nbsp;&nbsp;.&nbsp; | &nbsp;&nbsp;1&nbsp; | &nbsp;&nbsp;.&nbsp; | &nbsp;&nbsp;.&nbsp; | &nbsp;&nbsp;.&nbsp; | &nbsp;&nbsp;.&nbsp; | &nbsp;&nbsp;.&nbsp; | &nbsp;&nbsp;.&nbsp; | &nbsp;&nbsp;.&nbsp; | &nbsp;&nbsp;.&nbsp; | &nbsp;&nbsp;.&nbsp; | &nbsp;&nbsp;.&nbsp; | &nbsp;&nbsp;.&nbsp; | &nbsp;&nbsp;.&nbsp; | &nbsp;&nbsp;.&nbsp; | &nbsp;&nbsp;.&nbsp; | &nbsp;&nbsp;.&nbsp; | &nbsp;&nbsp;.&nbsp; | &nbsp;&nbsp;.&nbsp; |  &nbsp;&nbsp;1&nbsp; | &nbsp;&nbsp;DIYLB_carriage_B.stl |
| &nbsp;&nbsp;.&nbsp; | &nbsp;&nbsp;.&nbsp; | &nbsp;&nbsp;1&nbsp; | &nbsp;&nbsp;.&nbsp; | &nbsp;&nbsp;.&nbsp; | &nbsp;&nbsp;.&nbsp; | &nbsp;&nbsp;.&nbsp; | &nbsp;&nbsp;.&nbsp; | &nbsp;&nbsp;.&nbsp; | &nbsp;&nbsp;.&nbsp; | &nbsp;&nbsp;.&nbsp; | &nbsp;&nbsp;.&nbsp; | &nbsp;&nbsp;.&nbsp; | &nbsp;&nbsp;.&nbsp; | &nbsp;&nbsp;.&nbsp; | &nbsp;&nbsp;.&nbsp; | &nbsp;&nbsp;.&nbsp; | &nbsp;&nbsp;.&nbsp; | &nbsp;&nbsp;.&nbsp; | &nbsp;&nbsp;.&nbsp; | &nbsp;&nbsp;.&nbsp; | &nbsp;&nbsp;.&nbsp; |  &nbsp;&nbsp;1&nbsp; | &nbsp;&nbsp;DIYLB_carriage_C.stl |
| &nbsp;&nbsp;.&nbsp; | &nbsp;&nbsp;1&nbsp; | &nbsp;&nbsp;.&nbsp; | &nbsp;&nbsp;.&nbsp; | &nbsp;&nbsp;.&nbsp; | &nbsp;&nbsp;.&nbsp; | &nbsp;&nbsp;.&nbsp; | &nbsp;&nbsp;.&nbsp; | &nbsp;&nbsp;.&nbsp; | &nbsp;&nbsp;.&nbsp; | &nbsp;&nbsp;.&nbsp; | &nbsp;&nbsp;.&nbsp; | &nbsp;&nbsp;.&nbsp; | &nbsp;&nbsp;.&nbsp; | &nbsp;&nbsp;.&nbsp; | &nbsp;&nbsp;.&nbsp; | &nbsp;&nbsp;.&nbsp; | &nbsp;&nbsp;.&nbsp; | &nbsp;&nbsp;.&nbsp; | &nbsp;&nbsp;.&nbsp; | &nbsp;&nbsp;.&nbsp; | &nbsp;&nbsp;.&nbsp; |  &nbsp;&nbsp;1&nbsp; | &nbsp;&nbsp;DIYLB_carriage_D.stl |
| &nbsp;&nbsp;.&nbsp; | &nbsp;&nbsp;.&nbsp; | &nbsp;&nbsp;.&nbsp; | &nbsp;&nbsp;.&nbsp; | &nbsp;&nbsp;.&nbsp; | &nbsp;&nbsp;.&nbsp; | &nbsp;&nbsp;.&nbsp; | &nbsp;&nbsp;1&nbsp; | &nbsp;&nbsp;.&nbsp; | &nbsp;&nbsp;.&nbsp; | &nbsp;&nbsp;.&nbsp; | &nbsp;&nbsp;.&nbsp; | &nbsp;&nbsp;.&nbsp; | &nbsp;&nbsp;.&nbsp; | &nbsp;&nbsp;.&nbsp; | &nbsp;&nbsp;.&nbsp; | &nbsp;&nbsp;.&nbsp; | &nbsp;&nbsp;.&nbsp; | &nbsp;&nbsp;.&nbsp; | &nbsp;&nbsp;.&nbsp; | &nbsp;&nbsp;.&nbsp; | &nbsp;&nbsp;.&nbsp; |  &nbsp;&nbsp;1&nbsp; | &nbsp;&nbsp;DIYLB_crank.stl |
| &nbsp;&nbsp;.&nbsp; | &nbsp;&nbsp;.&nbsp; | &nbsp;&nbsp;.&nbsp; | &nbsp;&nbsp;.&nbsp; | &nbsp;&nbsp;.&nbsp; | &nbsp;&nbsp;.&nbsp; | &nbsp;&nbsp;.&nbsp; | &nbsp;&nbsp;2&nbsp; | &nbsp;&nbsp;.&nbsp; | &nbsp;&nbsp;.&nbsp; | &nbsp;&nbsp;.&nbsp; | &nbsp;&nbsp;.&nbsp; | &nbsp;&nbsp;.&nbsp; | &nbsp;&nbsp;.&nbsp; | &nbsp;&nbsp;.&nbsp; | &nbsp;&nbsp;.&nbsp; | &nbsp;&nbsp;.&nbsp; | &nbsp;&nbsp;.&nbsp; | &nbsp;&nbsp;.&nbsp; | &nbsp;&nbsp;.&nbsp; | &nbsp;&nbsp;.&nbsp; | &nbsp;&nbsp;.&nbsp; |  &nbsp;&nbsp;2&nbsp; | &nbsp;&nbsp;DIYLB_crank_bearing.stl |
| &nbsp;&nbsp;.&nbsp; | &nbsp;&nbsp;.&nbsp; | &nbsp;&nbsp;.&nbsp; | &nbsp;&nbsp;.&nbsp; | &nbsp;&nbsp;.&nbsp; | &nbsp;&nbsp;.&nbsp; | &nbsp;&nbsp;.&nbsp; | &nbsp;&nbsp;.&nbsp; | &nbsp;&nbsp;1&nbsp; | &nbsp;&nbsp;.&nbsp; | &nbsp;&nbsp;.&nbsp; | &nbsp;&nbsp;.&nbsp; | &nbsp;&nbsp;.&nbsp; | &nbsp;&nbsp;.&nbsp; | &nbsp;&nbsp;.&nbsp; | &nbsp;&nbsp;.&nbsp; | &nbsp;&nbsp;.&nbsp; | &nbsp;&nbsp;.&nbsp; | &nbsp;&nbsp;.&nbsp; | &nbsp;&nbsp;.&nbsp; | &nbsp;&nbsp;.&nbsp; | &nbsp;&nbsp;.&nbsp; |  &nbsp;&nbsp;1&nbsp; | &nbsp;&nbsp;DIYLB_idler.stl |
| &nbsp;&nbsp;.&nbsp; | &nbsp;&nbsp;.&nbsp; | &nbsp;&nbsp;.&nbsp; | &nbsp;&nbsp;.&nbsp; | &nbsp;&nbsp;.&nbsp; | &nbsp;&nbsp;.&nbsp; | &nbsp;&nbsp;.&nbsp; | &nbsp;&nbsp;.&nbsp; | &nbsp;&nbsp;.&nbsp; | &nbsp;&nbsp;4&nbsp; | &nbsp;&nbsp;.&nbsp; | &nbsp;&nbsp;.&nbsp; | &nbsp;&nbsp;.&nbsp; | &nbsp;&nbsp;.&nbsp; | &nbsp;&nbsp;.&nbsp; | &nbsp;&nbsp;.&nbsp; | &nbsp;&nbsp;.&nbsp; | &nbsp;&nbsp;.&nbsp; | &nbsp;&nbsp;.&nbsp; | &nbsp;&nbsp;.&nbsp; | &nbsp;&nbsp;.&nbsp; | &nbsp;&nbsp;.&nbsp; |  &nbsp;&nbsp;4&nbsp; | &nbsp;&nbsp;DIYLB_lower_bearing.stl |
| &nbsp;&nbsp;.&nbsp; | &nbsp;&nbsp;.&nbsp; | &nbsp;&nbsp;.&nbsp; | &nbsp;&nbsp;.&nbsp; | &nbsp;&nbsp;.&nbsp; | &nbsp;&nbsp;.&nbsp; | &nbsp;&nbsp;.&nbsp; | &nbsp;&nbsp;.&nbsp; | &nbsp;&nbsp;.&nbsp; | &nbsp;&nbsp;.&nbsp; | &nbsp;&nbsp;.&nbsp; | &nbsp;&nbsp;.&nbsp; | &nbsp;&nbsp;4&nbsp; | &nbsp;&nbsp;.&nbsp; | &nbsp;&nbsp;.&nbsp; | &nbsp;&nbsp;.&nbsp; | &nbsp;&nbsp;.&nbsp; | &nbsp;&nbsp;.&nbsp; | &nbsp;&nbsp;.&nbsp; | &nbsp;&nbsp;.&nbsp; | &nbsp;&nbsp;.&nbsp; | &nbsp;&nbsp;.&nbsp; |  &nbsp;&nbsp;4&nbsp; | &nbsp;&nbsp;DIYLB_magnet.stl |
| &nbsp;&nbsp;.&nbsp; | &nbsp;&nbsp;.&nbsp; | &nbsp;&nbsp;.&nbsp; | &nbsp;&nbsp;.&nbsp; | &nbsp;&nbsp;.&nbsp; | &nbsp;&nbsp;.&nbsp; | &nbsp;&nbsp;.&nbsp; | &nbsp;&nbsp;.&nbsp; | &nbsp;&nbsp;.&nbsp; | &nbsp;&nbsp;.&nbsp; | &nbsp;&nbsp;.&nbsp; | &nbsp;&nbsp;4&nbsp; | &nbsp;&nbsp;.&nbsp; | &nbsp;&nbsp;.&nbsp; | &nbsp;&nbsp;.&nbsp; | &nbsp;&nbsp;.&nbsp; | &nbsp;&nbsp;.&nbsp; | &nbsp;&nbsp;.&nbsp; | &nbsp;&nbsp;.&nbsp; | &nbsp;&nbsp;.&nbsp; | &nbsp;&nbsp;.&nbsp; | &nbsp;&nbsp;.&nbsp; |  &nbsp;&nbsp;4&nbsp; | &nbsp;&nbsp;DIYLB_magnet_cover.stl |
| &nbsp;&nbsp;.&nbsp; | &nbsp;&nbsp;.&nbsp; | &nbsp;&nbsp;.&nbsp; | &nbsp;&nbsp;.&nbsp; | &nbsp;&nbsp;.&nbsp; | &nbsp;&nbsp;.&nbsp; | &nbsp;&nbsp;4&nbsp; | &nbsp;&nbsp;.&nbsp; | &nbsp;&nbsp;.&nbsp; | &nbsp;&nbsp;.&nbsp; | &nbsp;&nbsp;.&nbsp; | &nbsp;&nbsp;.&nbsp; | &nbsp;&nbsp;.&nbsp; | &nbsp;&nbsp;.&nbsp; | &nbsp;&nbsp;.&nbsp; | &nbsp;&nbsp;.&nbsp; | &nbsp;&nbsp;.&nbsp; | &nbsp;&nbsp;.&nbsp; | &nbsp;&nbsp;.&nbsp; | &nbsp;&nbsp;.&nbsp; | &nbsp;&nbsp;.&nbsp; | &nbsp;&nbsp;.&nbsp; |  &nbsp;&nbsp;4&nbsp; | &nbsp;&nbsp;DIYLB_rail.stl |
| &nbsp;&nbsp;2&nbsp; | &nbsp;&nbsp;.&nbsp; | &nbsp;&nbsp;.&nbsp; | &nbsp;&nbsp;.&nbsp; | &nbsp;&nbsp;.&nbsp; | &nbsp;&nbsp;.&nbsp; | &nbsp;&nbsp;.&nbsp; | &nbsp;&nbsp;.&nbsp; | &nbsp;&nbsp;.&nbsp; | &nbsp;&nbsp;.&nbsp; | &nbsp;&nbsp;.&nbsp; | &nbsp;&nbsp;.&nbsp; | &nbsp;&nbsp;.&nbsp; | &nbsp;&nbsp;.&nbsp; | &nbsp;&nbsp;.&nbsp; | &nbsp;&nbsp;.&nbsp; | &nbsp;&nbsp;.&nbsp; | &nbsp;&nbsp;.&nbsp; | &nbsp;&nbsp;.&nbsp; | &nbsp;&nbsp;.&nbsp; | &nbsp;&nbsp;.&nbsp; | &nbsp;&nbsp;.&nbsp; |  &nbsp;&nbsp;2&nbsp; | &nbsp;&nbsp;DIYLB_top_A.stl |
| &nbsp;&nbsp;2&nbsp; | &nbsp;&nbsp;.&nbsp; | &nbsp;&nbsp;.&nbsp; | &nbsp;&nbsp;.&nbsp; | &nbsp;&nbsp;.&nbsp; | &nbsp;&nbsp;.&nbsp; | &nbsp;&nbsp;.&nbsp; | &nbsp;&nbsp;.&nbsp; | &nbsp;&nbsp;.&nbsp; | &nbsp;&nbsp;.&nbsp; | &nbsp;&nbsp;.&nbsp; | &nbsp;&nbsp;.&nbsp; | &nbsp;&nbsp;.&nbsp; | &nbsp;&nbsp;.&nbsp; | &nbsp;&nbsp;.&nbsp; | &nbsp;&nbsp;.&nbsp; | &nbsp;&nbsp;.&nbsp; | &nbsp;&nbsp;.&nbsp; | &nbsp;&nbsp;.&nbsp; | &nbsp;&nbsp;.&nbsp; | &nbsp;&nbsp;.&nbsp; | &nbsp;&nbsp;.&nbsp; |  &nbsp;&nbsp;2&nbsp; | &nbsp;&nbsp;DIYLB_top_B.stl |
| &nbsp;&nbsp;4&nbsp; | &nbsp;&nbsp;1&nbsp; | &nbsp;&nbsp;1&nbsp; | &nbsp;&nbsp;.&nbsp; | &nbsp;&nbsp;1&nbsp; | &nbsp;&nbsp;1&nbsp; | &nbsp;&nbsp;4&nbsp; | &nbsp;&nbsp;3&nbsp; | &nbsp;&nbsp;1&nbsp; | &nbsp;&nbsp;4&nbsp; | &nbsp;&nbsp;.&nbsp; | &nbsp;&nbsp;4&nbsp; | &nbsp;&nbsp;4&nbsp; | &nbsp;&nbsp;.&nbsp; | &nbsp;&nbsp;.&nbsp; | &nbsp;&nbsp;.&nbsp; | &nbsp;&nbsp;.&nbsp; | &nbsp;&nbsp;.&nbsp; | &nbsp;&nbsp;.&nbsp; | &nbsp;&nbsp;8&nbsp; | &nbsp;&nbsp;.&nbsp; | &nbsp;&nbsp;.&nbsp; | &nbsp;&nbsp;36&nbsp; | &nbsp;&nbsp;Total 3D printed parts count |

<span></span>
[Top](#TOP)

---

## 2 x DIYLB Top Assembly
### Vitamins
|Qty|Description|
|---:|:---|
|4| Screw M6 cap x 20mm|
|4| Washer  M6 x 12.5mm x 1.5mm|

### 3D Printed parts

| 2 x DIYLB_top_A.stl | 2 x DIYLB_top_B.stl |
|---|---|
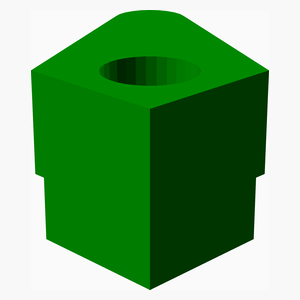
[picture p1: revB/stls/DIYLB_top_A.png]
DIYLB_top_A.stl
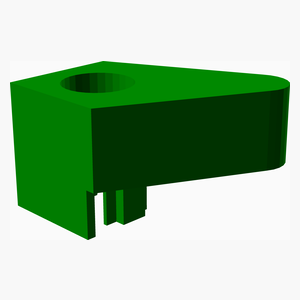
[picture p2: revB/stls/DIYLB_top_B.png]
DIYLB_top_B.stl
|  |  

### Assembly instructions
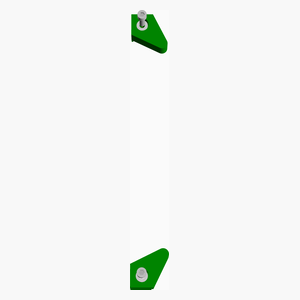
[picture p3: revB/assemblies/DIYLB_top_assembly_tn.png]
DIYLB_top_assembly


1. Cut a M6 thread into the top of the vertical 20x20 extrusions 
2. Attach the top holders
3. Secure the top holders with M6 screws

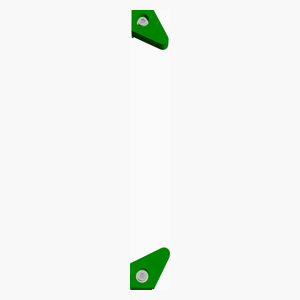
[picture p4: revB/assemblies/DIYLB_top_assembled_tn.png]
DIYLB_top_assembled


<span></span>
[Top](#TOP)

---

## DIYLB Carriage D Assembly
### Vitamins
|Qty|Description|
|---:|:---|
|1| Linear rail carriage MGN7C|
|2| Nut M3 x 2.4mm |
|4| Screw M2 cap x 10mm|
|2| Screw M3 pan x 12mm|
|1| Screw M4 cap x 12mm|
|1| Screw M6 pan x 20mm|
|1| T-Nut (20x20)|
|1| T8-Nut (narrow)|
|4| Washer  M2 x 5mm x 0.3mm|
|1| Washer  M4 x 9mm x 0.8mm|
|1| Washer  M6 x 12.5mm x 1.5mm|

### 3D Printed parts

| 1 x DIYLB_carriage_D.stl |
|---|
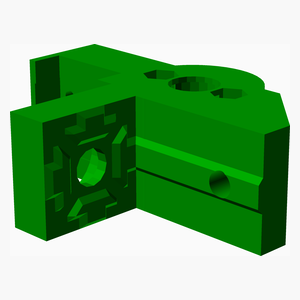
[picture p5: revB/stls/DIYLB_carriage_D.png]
DIYLB_carriage_D.stl
|  

### Assembly instructions
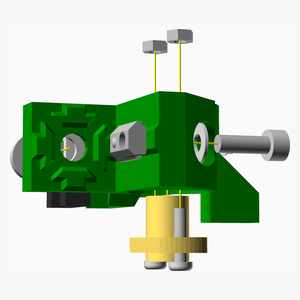
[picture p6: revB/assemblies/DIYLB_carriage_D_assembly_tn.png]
DIYLB_carriage_D_assembly


1. Attatch T8-nut to the carriage holder, using M3 screws,
2. Attatch the rail carriage to the carriage holder using M2 screws.
3. Put a T-nuts into the mounting hole.

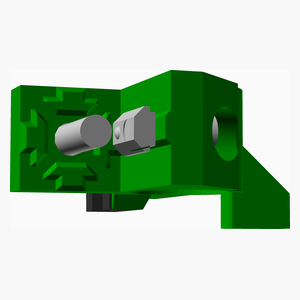
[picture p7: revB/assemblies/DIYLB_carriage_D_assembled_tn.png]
DIYLB_carriage_D_assembled


<span></span>
[Top](#TOP)

---

## DIYLB Carriage C Assembly
### Vitamins
|Qty|Description|
|---:|:---|
|1| Linear rail carriage MGN7C|
|2| Nut M3 x 2.4mm |
|4| Screw M2 cap x 10mm|
|2| Screw M3 pan x 12mm|
|1| Screw M4 cap x 12mm|
|1| Screw M6 pan x 20mm|
|1| T-Nut (20x20)|
|1| T8-Nut (narrow)|
|4| Washer  M2 x 5mm x 0.3mm|
|1| Washer  M4 x 9mm x 0.8mm|
|1| Washer  M6 x 12.5mm x 1.5mm|

### 3D Printed parts

| 1 x DIYLB_carriage_C.stl |
|---|
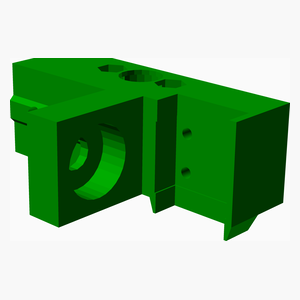
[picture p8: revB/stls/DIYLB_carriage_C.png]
DIYLB_carriage_C.stl
|  

### Assembly instructions
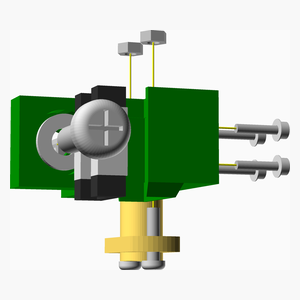
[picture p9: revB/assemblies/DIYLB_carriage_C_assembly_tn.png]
DIYLB_carriage_C_assembly


1. Attatch T8-nut to the carriage holder, using M3 screws,
2. Attatch the rail carriage to the carriage holder using M2 screws.
3. Put a T-nuts into the mounting hole.

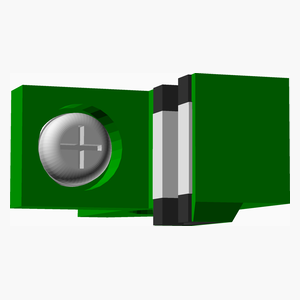
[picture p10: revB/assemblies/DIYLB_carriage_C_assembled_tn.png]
DIYLB_carriage_C_assembled


<span></span>
[Top](#TOP)

---

## 2 x DIYLB Carriage AB Assembly
### Vitamins
|Qty|Description|
|---:|:---|
|2| Extrusion E2020 x 235mm|

### Sub-assemblies

| 1 x DIYLB_carriage_A_assembly | 1 x DIYLB_carriage_B_assembly | 1 x DIYLB_carriage_C_assembly |
|---|---|---|
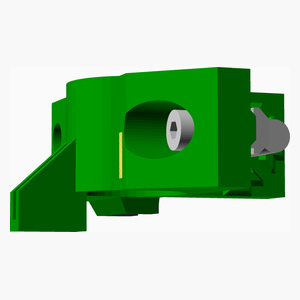
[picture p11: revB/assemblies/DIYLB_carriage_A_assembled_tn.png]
DIYLB_carriage_A_assembled
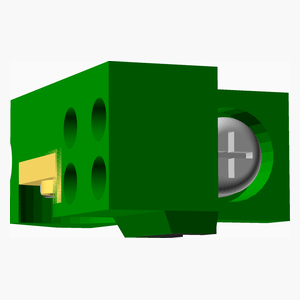
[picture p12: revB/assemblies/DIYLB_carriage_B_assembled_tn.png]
DIYLB_carriage_B_assembled
|  |  | DIYLB_carriage_C_assembled 

| 1 x DIYLB_carriage_D_assembly |
|---|
| DIYLB_carriage_D_assembled 

### Assembly instructions
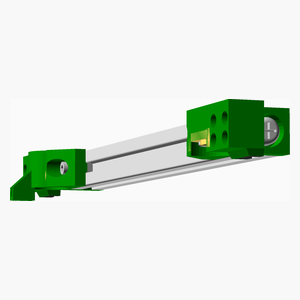
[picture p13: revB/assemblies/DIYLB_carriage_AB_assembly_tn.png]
DIYLB_carriage_AB_assembly


1. Cut a M6 thread into both ends of the extrusion,
2. Attatch attxh the carriage holders

DIYLB_carriage_AB_assembled

<span></span>
[Top](#TOP)

---

## DIYLB Carriage B Assembly
### Vitamins
|Qty|Description|
|---:|:---|
|1| Linear rail carriage MGN7C|
|2| Nut M3 x 2.4mm |
|4| Screw M2 cap x 10mm|
|2| Screw M3 pan x 12mm|
|1| Screw M4 cap x 12mm|
|1| Screw M6 pan x 20mm|
|1| T-Nut (20x20)|
|1| T8-Nut (narrow)|
|4| Washer  M2 x 5mm x 0.3mm|
|1| Washer  M4 x 9mm x 0.8mm|
|1| Washer  M6 x 12.5mm x 1.5mm|

### 3D Printed parts

| 1 x DIYLB_carriage_B.stl |
|---|
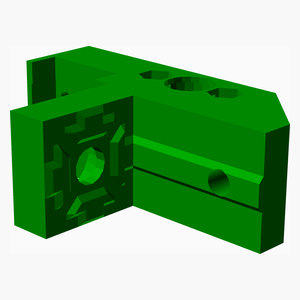
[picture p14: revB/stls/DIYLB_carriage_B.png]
DIYLB_carriage_B.stl
|  

### Assembly instructions
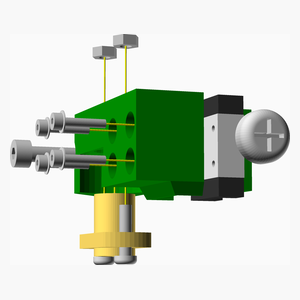
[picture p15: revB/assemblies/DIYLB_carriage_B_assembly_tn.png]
DIYLB_carriage_B_assembly


1. Attatch T8-nut to the carriage holder, using M3 screws,
2. Attatch the rail carriage to the carriage holder using M2 screws.
3. Put a T-nuts into the mounting hole.

DIYLB_carriage_B_assembled

<span></span>
[Top](#TOP)

---

## DIYLB Carriage A Assembly
### Vitamins
|Qty|Description|
|---:|:---|
|1| Linear rail carriage MGN7C|
|2| Nut M3 x 2.4mm |
|4| Screw M2 cap x 10mm|
|2| Screw M3 pan x 12mm|
|1| Screw M4 cap x 12mm|
|1| Screw M6 pan x 20mm|
|1| T-Nut (20x20)|
|1| T8-Nut (narrow)|
|4| Washer  M2 x 5mm x 0.3mm|
|1| Washer  M4 x 9mm x 0.8mm|
|1| Washer  M6 x 12.5mm x 1.5mm|

### 3D Printed parts

| 1 x DIYLB_carriage_A.stl |
|---|
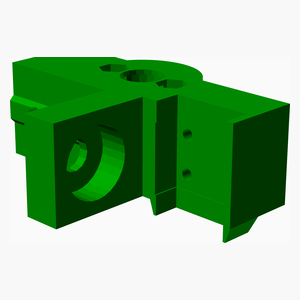
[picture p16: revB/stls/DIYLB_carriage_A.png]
DIYLB_carriage_A.stl
|  

### Assembly instructions
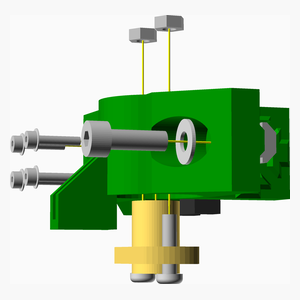
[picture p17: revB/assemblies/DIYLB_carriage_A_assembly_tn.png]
DIYLB_carriage_A_assembly


1. Attatch T8-nut to the carriage holder, using M3 screws,
2. Attatch the rail carriage to the carriage holder using M2 screws.
3. Put a T-nuts into the mounting hole.

DIYLB_carriage_A_assembled

<span></span>
[Top](#TOP)

---

## 4 x DIYLB Rail Assembly
### Vitamins
|Qty|Description|
|---:|:---|
|4| Extrusion E2020 x 70mm|
|4| Linear rail MGN7 x 70mm|
|20| Nut M2 x 1.6mm |
|20| Screw M2 cap x  6mm|

### 3D Printed parts

| 4 x DIYLB_rail.stl |
|---|
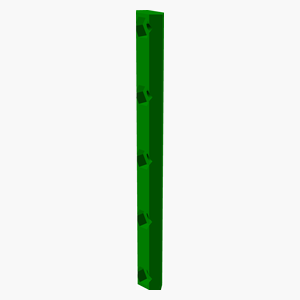
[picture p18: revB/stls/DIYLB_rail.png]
DIYLB_rail.stl
|  

### Assembly instructions
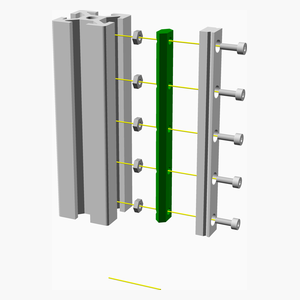
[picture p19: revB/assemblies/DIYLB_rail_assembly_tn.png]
DIYLB_rail_assembly


1. Insert the M2 nuts into the printed holder.
2. Attach the rail loosely.
3. Slide the printed holder into the 20x20 extrusion and tighten the screws.

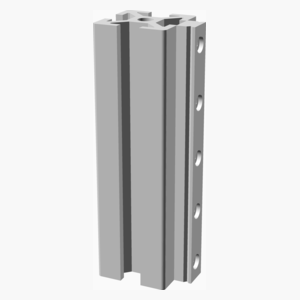
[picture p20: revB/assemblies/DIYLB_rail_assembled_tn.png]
DIYLB_rail_assembled


<span></span>
[Top](#TOP)

---

## DIYLB Crank Assembly
### Vitamins
|Qty|Description|
|---:|:---|
|2| Ball bearing 608-2RS 8mm x 22mm x 7mm|
|1| Extrusion E2040 x 60mm|
|1| Extrusion E2040 x 70mm|
|2| L-Bracket (20x20)|
|1| Nut M8 x 6.5mm |
|2| Pulley GT2 idler smooth 12mm|
|1| Pulley GT2OB 20 teeth|
|6| Screw M3 grub x  6mm|
|2| Screw M4 cap x 15mm|
|4| Screw M4 dome x  8mm|
|3| Screw M8 hex x 50mm|
|4| T-Nut (20x20)|
|2| T-Nut (20x20)|
|6| Washer  M4 x 9mm x 0.8mm|

### 3D Printed parts

| 1 x DIYLB_crank.stl | 2 x DIYLB_crank_bearing.stl |
|---|---|
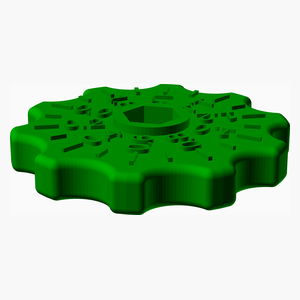
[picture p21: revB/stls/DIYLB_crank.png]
DIYLB_crank.stl
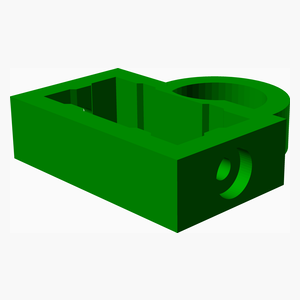
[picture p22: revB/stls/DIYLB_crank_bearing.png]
DIYLB_crank_bearing.stl
|  |  

### Assembly instructions
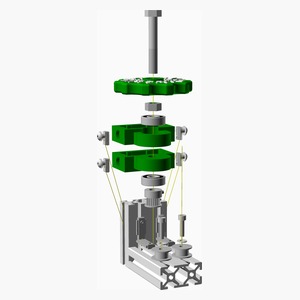
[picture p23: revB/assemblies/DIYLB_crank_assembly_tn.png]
DIYLB_crank_assembly


1. Connect the two 20x40 extrusions with L-brackets.
2. Assemble the axis as illustrated.
3. Slide the printed holders over the vertical 20x40 extrusion
   (and loosely insert the timing belt).
4. Move the two printed holders as far apart as possible and tighten the screws.
5. Slide two idlers on T-nuts onto the top slot of the horizontal 20x40 extrusion.

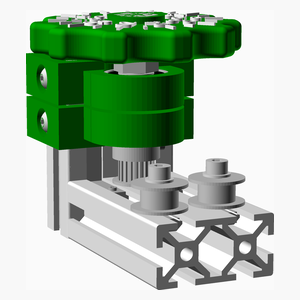
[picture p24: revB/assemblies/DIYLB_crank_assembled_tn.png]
DIYLB_crank_assembled


<span></span>
[Top](#TOP)

---

## DIYLB Idler Assembly
### Vitamins
|Qty|Description|
|---:|:---|
|1| Nut M5 x 4mm |
|1| Pulley GT2 idler 20 teeth|
|2| Screw M4 cap x 12mm|
|1| Screw M5 cap x 28mm|
|2| T-Nut (20x20)|
|2| Washer  M4 x 9mm x 0.8mm|
|1| Washer  M5 x 10mm x 1mm|

### 3D Printed parts

| 1 x DIYLB_idler.stl |
|---|
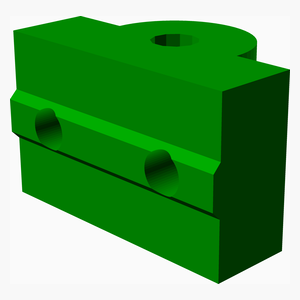
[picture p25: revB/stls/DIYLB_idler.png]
DIYLB_idler.stl
|  

### Assembly instructions
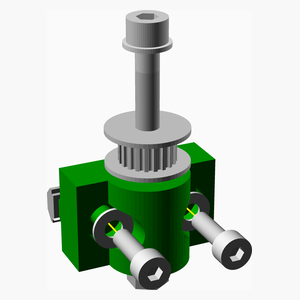
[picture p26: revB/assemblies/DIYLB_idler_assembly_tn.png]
DIYLB_idler_assembly


1. Screw the idler onto the holder.
2. Attach two T-nuts with screws and washers.

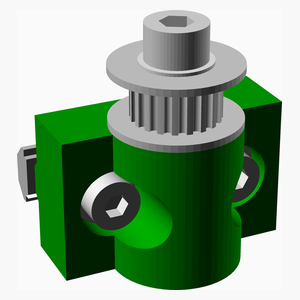
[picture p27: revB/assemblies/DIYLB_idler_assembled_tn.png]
DIYLB_idler_assembled


<span></span>
[Top](#TOP)

---

## 4 x DIYLB Lower Bearing Assembly
### Vitamins
|Qty|Description|
|---:|:---|
|4| Ball bearing 608-2RS 8mm x 22mm x 7mm|
|4| Euro-Cent coin|
|4| Pulley GT2OB 20 teeth|
|8| Screw M3 grub x  6mm|
|8| Screw M4 cap x 12mm|
|8| T-Nut (20x20)|
|4| Threaded rod M8 x 100mm|
|8| Washer  M4 x 9mm x 0.8mm|

### 3D Printed parts

| 4 x DIYLB_lower_bearing.stl |
|---|
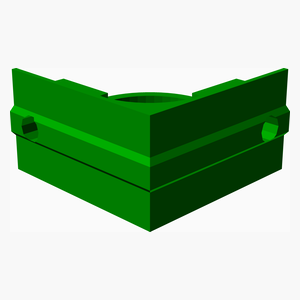
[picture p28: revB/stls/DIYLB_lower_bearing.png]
DIYLB_lower_bearing.stl
|  

### Assembly instructions
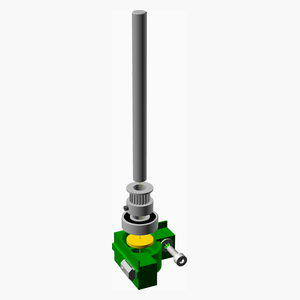
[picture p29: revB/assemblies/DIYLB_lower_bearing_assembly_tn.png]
DIYLB_lower_bearing_assembly


1. Put a EuroCent coin in the bottom of the lower ball bearing holder.
2. Squeze the ball bearing into the holder.
3. Attach two T-nuts with screws and washers.
4. Put the pulley loosely onto the threaded rod and insert them into the ball bearingpulles.  

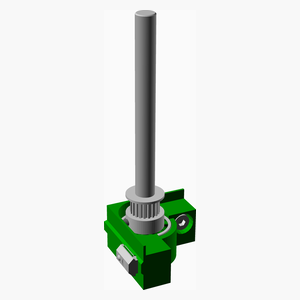
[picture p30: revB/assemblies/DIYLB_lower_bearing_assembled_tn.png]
DIYLB_lower_bearing_assembled


<span></span>
[Top](#TOP)

---

## DIYLB Base Right Assembly
### Vitamins
|Qty|Description|
|---:|:---|
|1| Extrusion E2020 x 300mm|
|2| L-Bracket (20x20)|
|4| Screw M3 grub x  6mm|

### Sub-assemblies

| 1 x DIYLB_idler_assembly | 2 x DIYLB_lower_bearing_assembly |
|---|---|
| DIYLB_idler_assembled | DIYLB_lower_bearing_assembled 

### Assembly instructions
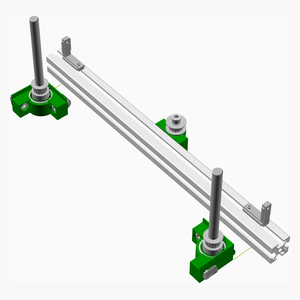
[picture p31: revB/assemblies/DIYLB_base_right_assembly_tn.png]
DIYLB_base_right_assembly


1. Slide two L-brackets onto the top slot of the 20x20 extrusion.
2. Slide the two holders for the ball bearings onto the lef-thand slot
   of the 20x20 extrusion.
3. Attach the idler mount

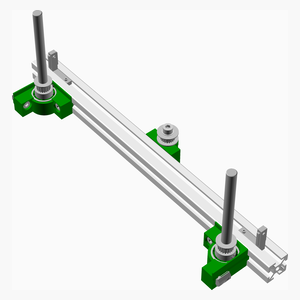
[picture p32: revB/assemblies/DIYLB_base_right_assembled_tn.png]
DIYLB_base_right_assembled


<span></span>
[Top](#TOP)

---

## 4 x DIYLB Magnet Cover Assembly
### Vitamins
|Qty|Description|
|---:|:---|
|4| Euro-Cent coin|

### 3D Printed parts

| 4 x DIYLB_magnet_cover.stl |
|---|
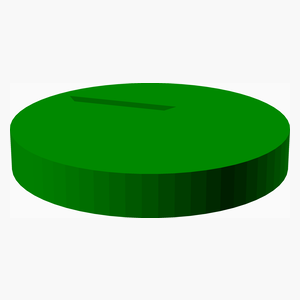
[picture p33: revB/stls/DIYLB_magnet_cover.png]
DIYLB_magnet_cover.stl
|  

### Assembly instructions
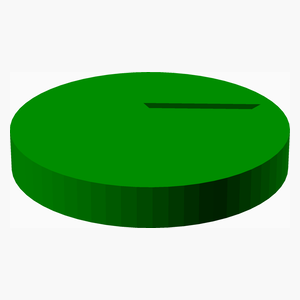
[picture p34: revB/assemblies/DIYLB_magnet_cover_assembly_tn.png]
DIYLB_magnet_cover_assembly


1. insert cent coin during print.

DIYLB_magnet_cover_assembled

<span></span>
[Top](#TOP)

---

## 4 x DIYLB Magnet Assembly
### Vitamins
|Qty|Description|
|---:|:---|
|4| Neodym Magnet (D=20,H=4.5)|
|8| Screw M4 cap x 12mm|
|8| T-Nut (20x20)|
|8| Washer  M4 x 9mm x 0.8mm|

### 3D Printed parts

| 4 x DIYLB_magnet.stl |
|---|
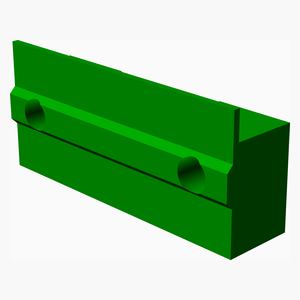
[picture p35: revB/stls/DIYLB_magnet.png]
DIYLB_magnet.stl
|  

### Sub-assemblies

| 4 x DIYLB_magnet_cover_assembly |
|---|
| DIYLB_magnet_cover_assembled 

### Assembly instructions
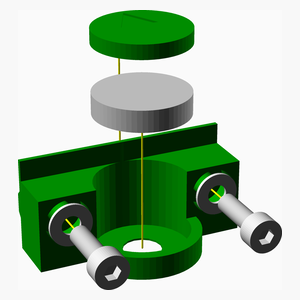
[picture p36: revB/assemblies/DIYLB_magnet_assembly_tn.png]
DIYLB_magnet_assembly


1. Squeze the magnet into the holder.
2. Attach two T-nuts with screws and washers.
3. Put the covers on top of the magnets.

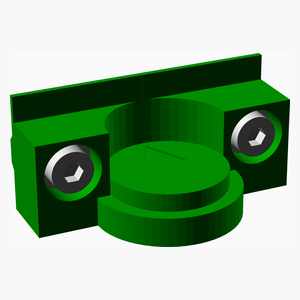
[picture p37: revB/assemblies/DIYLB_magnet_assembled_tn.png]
DIYLB_magnet_assembled


<span></span>
[Top](#TOP)

---

## 2 x DIYLB Base Center Assembly
### Vitamins
|Qty|Description|
|---:|:---|
|2| Extrusion E2020 x 320mm|

### Sub-assemblies

| 4 x DIYLB_magnet_assembly |
|---|
| DIYLB_magnet_assembled 

### Assembly instructions
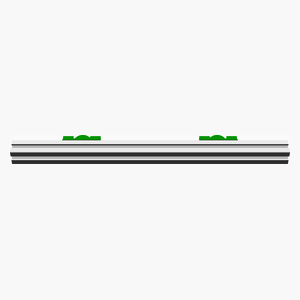
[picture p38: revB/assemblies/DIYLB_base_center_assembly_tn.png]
DIYLB_base_center_assembly


1. Attach two magnet holders to the 320mm 20x20 extrusion.

DIYLB_base_center_assembled

<span></span>
[Top](#TOP)

---

## DIYLB Base Left Assembly
### Vitamins
|Qty|Description|
|---:|:---|
|1| Extrusion E2020 x 300mm|
|4| L-Bracket (20x20)|
|8| Screw M3 grub x  6mm|

### Sub-assemblies

| 2 x DIYLB_lower_bearing_assembly |
|---|
| DIYLB_lower_bearing_assembled 

### Assembly instructions
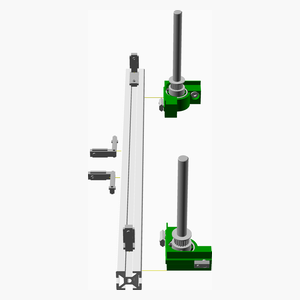
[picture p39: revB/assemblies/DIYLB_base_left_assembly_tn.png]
DIYLB_base_left_assembly


1. Slide two L-brackets onto the top slot of the 20x20 extrusion.
2. Slide the two holders for the ball bearings onto the right-hand slot
   of the 20x20 extrusion.
3. Slide two L-brackets onto the left-hand slot of the 20x20 extrusion.

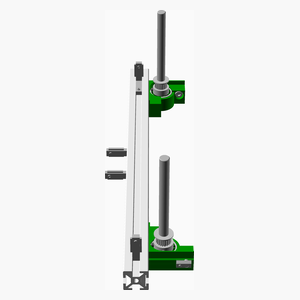
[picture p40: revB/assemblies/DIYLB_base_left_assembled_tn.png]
DIYLB_base_left_assembled


<span></span>
[Top](#TOP)

---

## DIYLB Base Assembly
### Sub-assemblies

| 2 x DIYLB_base_center_assembly | 1 x DIYLB_base_left_assembly | 1 x DIYLB_base_right_assembly |
|---|---|---|
| DIYLB_base_center_assembled | DIYLB_base_left_assembled | DIYLB_base_right_assembled 

### Assembly instructions
DIYLB_Base_assembly

1. Attach all parts of the base frame
2. Tighten the screws of the bearing holders, connecting 20x20 extrusions

DIYLB_Base_assembled

<span></span>
[Top](revB/#TOP)

---

## DIYLB Crank To Base Assembly
### Sub-assemblies

| 1 x DIYLB_Base_assembly | 1 x DIYLB_crank_assembly |
|---|---|
| DIYLB_Base_assembled | DIYLB_crank_assembled 

### Assembly instructions
DIYLB_crank_to_base_assembly

1. Attach the crank holder to the base of the frame  
2. Tighten the screws of the L-brackets

DIYLB_crank_to_base_assembled

<span></span>
[Top](#TOP)

---

## DIYLB Columns To Base Assembly
### Sub-assemblies

| 1 x DIYLB_crank_to_base_assembly | 4 x DIYLB_rail_assembly |
|---|---|
| DIYLB_crank_to_base_assembled | DIYLB_rail_assembled 

### Assembly instructions
DIYLB_columns_to_base_assembly

1. Attach the for columns to the base of the frame  
2. Tighten the screws of the L-brackets

DIYLB_columns_to_base_assembled

<span></span>
[Top](#TOP)

---

## DIYLB Bed To Columns Assembly
### Sub-assemblies

| 2 x DIYLB_carriage_AB_assembly | 1 x DIYLB_columns_to_base_assembly |
|---|---|
| DIYLB_carriage_AB_assembled | DIYLB_columns_to_base_assembled 

### Assembly instructions
DIYLB_bed_to_columns_assembly

1. Thread the assembled carriage holders into the rails and rods of the Z-axis.

DIYLB_bed_to_columns_assembled

<span></span>
[Top](#TOP)

---

## DIYLB Beams To Bed Assembly
### Vitamins
|Qty|Description|
|---:|:---|
|1| Flat section 15mmx2mm, 272mm|
|4| Flat section 15mmx2mm, 316mm|

### 3D Printed parts

| 8 x DIYLB_beam_holder.stl |
|---|
| DIYLB_beam_holder.stl 

### Sub-assemblies

| 1 x DIYLB_bed_to_columns_assembly |
|---|
| DIYLB_bed_to_columns_assembled 

### Assembly instructions
DIYLB_beams_to_bed_assembly

1. Attach the beam holders to the horizontal 20x20 extrusions of the bed.
2. Slide the beams into the beam holders

DIYLB_beams_to_bed_assembled

<span></span>
[Top](#TOP)

---

## DIYLB Top To Columns Assembly
### Sub-assemblies

| 1 x DIYLB_beams_to_bed_assembly | 2 x DIYLB_top_assembly |
|---|---|
| DIYLB_beams_to_bed_assembled | DIYLB_top_assembled 

### Assembly instructions
DIYLB_top_to_columns_assembly

1. Attach the top extrusions to the rest of the frame.

DIYLB_top_to_columns_assembled

<span></span>
[Top](#TOP)

---

## DIYLB Belt Assembly
### Vitamins
|Qty|Description|
|---:|:---|
|1| Belt GT2 x 6mm x 1222mm|

### Sub-assemblies

| 1 x DIYLB_top_to_columns_assembly |
|---|
| DIYLB_top_to_columns_assembled 

### Assembly instructions
DIYLB_belt_assembly

1. Insert the timing belt
2. Level the bed by turning the thraded rods, before tightening the pulleys 

DIYLB_belt_assembled

<span></span>
[Top](#TOP)

---
Finished!

<span></span>
[Top](#TOP)

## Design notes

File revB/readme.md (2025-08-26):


# RevB
This is a DIY laser bed for K40 cutters and clones.
inside

<span></span>

---
## Table of Contents
1. [Parts list](#Parts_list)
1. [DIYLB Top Assembly](#DIYLB_top_assembly)
1. [DIYLB Carriage D Assembly](#DIYLB_carriage_D_assembly)
1. [DIYLB Carriage C Assembly](#DIYLB_carriage_C_assembly)
1. [DIYLB Carriage AB Assembly](#DIYLB_carriage_AB_assembly)
1. [DIYLB Carriage B Assembly](#DIYLB_carriage_B_assembly)
1. [DIYLB Carriage A Assembly](#DIYLB_carriage_A_assembly)
1. [DIYLB Rail Assembly](#DIYLB_rail_assembly)
1. [DIYLB Crank Assembly](#DIYLB_crank_assembly)
1. [DIYLB Idler Assembly](#DIYLB_idler_assembly)
1. [DIYLB Lower Bearing Assembly](#DIYLB_lower_bearing_assembly)
1. [DIYLB Base Right Assembly](#DIYLB_base_right_assembly)
1. [DIYLB Magnet Cover Assembly](#DIYLB_magnet_cover_assembly)
1. [DIYLB Magnet Assembly](#DIYLB_magnet_assembly)
1. [DIYLB Base Center Assembly](#DIYLB_base_center_assembly)
1. [DIYLB Base Left Assembly](#DIYLB_base_left_assembly)
1. [DIYLB Base Assembly](#DIYLB_Base_assembly)
1. [DIYLB Crank To Base Assembly](#DIYLB_crank_to_base_assembly)
1. [DIYLB Columns To Base Assembly](#DIYLB_columns_to_base_assembly)
1. [DIYLB Bed To Columns Assembly](#DIYLB_bed_to_columns_assembly)
1. [DIYLB Beams To Bed Assembly](#DIYLB_beams_to_bed_assembly)
1. [DIYLB Top To Columns Assembly](#DIYLB_top_to_columns_assembly)
1. [DIYLB Belt Assembly](#DIYLB_belt_assembly)

<span></span>
[Top](#TOP)

---

## Parts list
| <span style="writing-mode: vertical-rl; text-orientation: mixed;">2 x DIYLB&nbsp;Top</span> | <span style="writing-mode: vertical-rl; text-orientation: mixed;">DIYLB&nbsp;Carriage&nbsp;D</span> | <span style="writing-mode: vertical-rl; text-orientation: mixed;">DIYLB&nbsp;Carriage&nbsp;C</span> | <span style="writing-mode: vertical-rl; text-orientation: mixed;">2 x DIYLB&nbsp;Carriage&nbsp;AB</span> | <span style="writing-mode: vertical-rl; text-orientation: mixed;">DIYLB&nbsp;Carriage&nbsp;B</span> | <span style="writing-mode: vertical-rl; text-orientation: mixed;">DIYLB&nbsp;Carriage&nbsp;A</span> | <span style="writing-mode: vertical-rl; text-orientation: mixed;">4 x DIYLB&nbsp;Rail</span> | <span style="writing-mode: vertical-rl; text-orientation: mixed;">DIYLB&nbsp;Crank</span> | <span style="writing-mode: vertical-rl; text-orientation: mixed;">DIYLB&nbsp;Idler</span> | <span style="writing-mode: vertical-rl; text-orientation: mixed;">4 x DIYLB&nbsp;Lower&nbsp;Bearing</span> | <span style="writing-mode: vertical-rl; text-orientation: mixed;">DIYLB&nbsp;Base&nbsp;Right</span> | <span style="writing-mode: vertical-rl; text-orientation: mixed;">4 x DIYLB&nbsp;Magnet&nbsp;Cover</span> | <span style="writing-mode: vertical-rl; text-orientation: mixed;">4 x DIYLB&nbsp;Magnet</span> | <span style="writing-mode: vertical-rl; text-orientation: mixed;">2 x DIYLB&nbsp;Base&nbsp;Center</span> | <span style="writing-mode: vertical-rl; text-orientation: mixed;">DIYLB&nbsp;Base&nbsp;Left</span> | <span style="writing-mode: vertical-rl; text-orientation: mixed;">DIYLB&nbsp;Base</span> | <span style="writing-mode: vertical-rl; text-orientation: mixed;">DIYLB&nbsp;Crank&nbsp;To&nbsp;Base</span> | <span style="writing-mode: vertical-rl; text-orientation: mixed;">DIYLB&nbsp;Columns&nbsp;To&nbsp;Base</span> | <span style="writing-mode: vertical-rl; text-orientation: mixed;">DIYLB&nbsp;Bed&nbsp;To&nbsp;Columns</span> | <span style="writing-mode: vertical-rl; text-orientation: mixed;">DIYLB&nbsp;Beams&nbsp;To&nbsp;Bed</span> | <span style="writing-mode: vertical-rl; text-orientation: mixed;">DIYLB&nbsp;Top&nbsp;To&nbsp;Columns</span> | <span style="writing-mode: vertical-rl; text-orientation: mixed;">DIYLB&nbsp;Belt</span> | <span style="writing-mode: vertical-rl; text-orientation: mixed;">TOTALS</span> |  |
|---:|---:|---:|---:|---:|---:|---:|---:|---:|---:|---:|---:|---:|---:|---:|---:|---:|---:|---:|---:|---:|---:|---:|:---|
|  |  |  |  |  |  |  |  |  |  |  |  |  |  |  |  |  |  |  |  |  |  | | **Vitamins** |
| &nbsp;&nbsp;.&nbsp; | &nbsp;&nbsp;.&nbsp; | &nbsp;&nbsp;.&nbsp; | &nbsp;&nbsp;.&nbsp; | &nbsp;&nbsp;.&nbsp; | &nbsp;&nbsp;.&nbsp; | &nbsp;&nbsp;.&nbsp; | &nbsp;&nbsp;2&nbsp; | &nbsp;&nbsp;.&nbsp; | &nbsp;&nbsp;4&nbsp; | &nbsp;&nbsp;.&nbsp; | &nbsp;&nbsp;.&nbsp; | &nbsp;&nbsp;.&nbsp; | &nbsp;&nbsp;.&nbsp; | &nbsp;&nbsp;.&nbsp; | &nbsp;&nbsp;.&nbsp; | &nbsp;&nbsp;.&nbsp; | &nbsp;&nbsp;.&nbsp; | &nbsp;&nbsp;.&nbsp; | &nbsp;&nbsp;.&nbsp; | &nbsp;&nbsp;.&nbsp; | &nbsp;&nbsp;.&nbsp; |  &nbsp;&nbsp;6&nbsp; | &nbsp;&nbsp; Ball bearing 608-2RS 8mm x 22mm x 7mm |
| &nbsp;&nbsp;.&nbsp; | &nbsp;&nbsp;.&nbsp; | &nbsp;&nbsp;.&nbsp; | &nbsp;&nbsp;.&nbsp; | &nbsp;&nbsp;.&nbsp; | &nbsp;&nbsp;.&nbsp; | &nbsp;&nbsp;.&nbsp; | &nbsp;&nbsp;.&nbsp; | &nbsp;&nbsp;.&nbsp; | &nbsp;&nbsp;.&nbsp; | &nbsp;&nbsp;.&nbsp; | &nbsp;&nbsp;.&nbsp; | &nbsp;&nbsp;.&nbsp; | &nbsp;&nbsp;.&nbsp; | &nbsp;&nbsp;.&nbsp; | &nbsp;&nbsp;.&nbsp; | &nbsp;&nbsp;.&nbsp; | &nbsp;&nbsp;.&nbsp; | &nbsp;&nbsp;.&nbsp; | &nbsp;&nbsp;.&nbsp; | &nbsp;&nbsp;.&nbsp; | &nbsp;&nbsp;1&nbsp; |  &nbsp;&nbsp;1&nbsp; | &nbsp;&nbsp; Belt GT2 x 6mm x 1222mm |
| &nbsp;&nbsp;.&nbsp; | &nbsp;&nbsp;.&nbsp; | &nbsp;&nbsp;.&nbsp; | &nbsp;&nbsp;.&nbsp; | &nbsp;&nbsp;.&nbsp; | &nbsp;&nbsp;.&nbsp; | &nbsp;&nbsp;.&nbsp; | &nbsp;&nbsp;.&nbsp; | &nbsp;&nbsp;.&nbsp; | &nbsp;&nbsp;4&nbsp; | &nbsp;&nbsp;.&nbsp; | &nbsp;&nbsp;4&nbsp; | &nbsp;&nbsp;.&nbsp; | &nbsp;&nbsp;.&nbsp; | &nbsp;&nbsp;.&nbsp; | &nbsp;&nbsp;.&nbsp; | &nbsp;&nbsp;.&nbsp; | &nbsp;&nbsp;.&nbsp; | &nbsp;&nbsp;.&nbsp; | &nbsp;&nbsp;.&nbsp; | &nbsp;&nbsp;.&nbsp; | &nbsp;&nbsp;.&nbsp; |  &nbsp;&nbsp;8&nbsp; | &nbsp;&nbsp; Euro-Cent coin |
| &nbsp;&nbsp;.&nbsp; | &nbsp;&nbsp;.&nbsp; | &nbsp;&nbsp;.&nbsp; | &nbsp;&nbsp;2&nbsp; | &nbsp;&nbsp;.&nbsp; | &nbsp;&nbsp;.&nbsp; | &nbsp;&nbsp;.&nbsp; | &nbsp;&nbsp;.&nbsp; | &nbsp;&nbsp;.&nbsp; | &nbsp;&nbsp;.&nbsp; | &nbsp;&nbsp;.&nbsp; | &nbsp;&nbsp;.&nbsp; | &nbsp;&nbsp;.&nbsp; | &nbsp;&nbsp;.&nbsp; | &nbsp;&nbsp;.&nbsp; | &nbsp;&nbsp;.&nbsp; | &nbsp;&nbsp;.&nbsp; | &nbsp;&nbsp;.&nbsp; | &nbsp;&nbsp;.&nbsp; | &nbsp;&nbsp;.&nbsp; | &nbsp;&nbsp;.&nbsp; | &nbsp;&nbsp;.&nbsp; |  &nbsp;&nbsp;2&nbsp; | &nbsp;&nbsp; Extrusion E2020 x 235mm |
| &nbsp;&nbsp;.&nbsp; | &nbsp;&nbsp;.&nbsp; | &nbsp;&nbsp;.&nbsp; | &nbsp;&nbsp;.&nbsp; | &nbsp;&nbsp;.&nbsp; | &nbsp;&nbsp;.&nbsp; | &nbsp;&nbsp;.&nbsp; | &nbsp;&nbsp;.&nbsp; | &nbsp;&nbsp;.&nbsp; | &nbsp;&nbsp;.&nbsp; | &nbsp;&nbsp;1&nbsp; | &nbsp;&nbsp;.&nbsp; | &nbsp;&nbsp;.&nbsp; | &nbsp;&nbsp;.&nbsp; | &nbsp;&nbsp;1&nbsp; | &nbsp;&nbsp;.&nbsp; | &nbsp;&nbsp;.&nbsp; | &nbsp;&nbsp;.&nbsp; | &nbsp;&nbsp;.&nbsp; | &nbsp;&nbsp;.&nbsp; | &nbsp;&nbsp;.&nbsp; | &nbsp;&nbsp;.&nbsp; |  &nbsp;&nbsp;2&nbsp; | &nbsp;&nbsp; Extrusion E2020 x 300mm |
| &nbsp;&nbsp;.&nbsp; | &nbsp;&nbsp;.&nbsp; | &nbsp;&nbsp;.&nbsp; | &nbsp;&nbsp;.&nbsp; | &nbsp;&nbsp;.&nbsp; | &nbsp;&nbsp;.&nbsp; | &nbsp;&nbsp;.&nbsp; | &nbsp;&nbsp;.&nbsp; | &nbsp;&nbsp;.&nbsp; | &nbsp;&nbsp;.&nbsp; | &nbsp;&nbsp;.&nbsp; | &nbsp;&nbsp;.&nbsp; | &nbsp;&nbsp;.&nbsp; | &nbsp;&nbsp;2&nbsp; | &nbsp;&nbsp;.&nbsp; | &nbsp;&nbsp;.&nbsp; | &nbsp;&nbsp;.&nbsp; | &nbsp;&nbsp;.&nbsp; | &nbsp;&nbsp;.&nbsp; | &nbsp;&nbsp;.&nbsp; | &nbsp;&nbsp;.&nbsp; | &nbsp;&nbsp;.&nbsp; |  &nbsp;&nbsp;2&nbsp; | &nbsp;&nbsp; Extrusion E2020 x 320mm |
| &nbsp;&nbsp;.&nbsp; | &nbsp;&nbsp;.&nbsp; | &nbsp;&nbsp;.&nbsp; | &nbsp;&nbsp;.&nbsp; | &nbsp;&nbsp;.&nbsp; | &nbsp;&nbsp;.&nbsp; | &nbsp;&nbsp;4&nbsp; | &nbsp;&nbsp;.&nbsp; | &nbsp;&nbsp;.&nbsp; | &nbsp;&nbsp;.&nbsp; | &nbsp;&nbsp;.&nbsp; | &nbsp;&nbsp;.&nbsp; | &nbsp;&nbsp;.&nbsp; | &nbsp;&nbsp;.&nbsp; | &nbsp;&nbsp;.&nbsp; | &nbsp;&nbsp;.&nbsp; | &nbsp;&nbsp;.&nbsp; | &nbsp;&nbsp;.&nbsp; | &nbsp;&nbsp;.&nbsp; | &nbsp;&nbsp;.&nbsp; | &nbsp;&nbsp;.&nbsp; | &nbsp;&nbsp;.&nbsp; |  &nbsp;&nbsp;4&nbsp; | &nbsp;&nbsp; Extrusion E2020 x 70mm |
| &nbsp;&nbsp;.&nbsp; | &nbsp;&nbsp;.&nbsp; | &nbsp;&nbsp;.&nbsp; | &nbsp;&nbsp;.&nbsp; | &nbsp;&nbsp;.&nbsp; | &nbsp;&nbsp;.&nbsp; | &nbsp;&nbsp;.&nbsp; | &nbsp;&nbsp;1&nbsp; | &nbsp;&nbsp;.&nbsp; | &nbsp;&nbsp;.&nbsp; | &nbsp;&nbsp;.&nbsp; | &nbsp;&nbsp;.&nbsp; | &nbsp;&nbsp;.&nbsp; | &nbsp;&nbsp;.&nbsp; | &nbsp;&nbsp;.&nbsp; | &nbsp;&nbsp;.&nbsp; | &nbsp;&nbsp;.&nbsp; | &nbsp;&nbsp;.&nbsp; | &nbsp;&nbsp;.&nbsp; | &nbsp;&nbsp;.&nbsp; | &nbsp;&nbsp;.&nbsp; | &nbsp;&nbsp;.&nbsp; |  &nbsp;&nbsp;1&nbsp; | &nbsp;&nbsp; Extrusion E2040 x 60mm |
| &nbsp;&nbsp;.&nbsp; | &nbsp;&nbsp;.&nbsp; | &nbsp;&nbsp;.&nbsp; | &nbsp;&nbsp;.&nbsp; | &nbsp;&nbsp;.&nbsp; | &nbsp;&nbsp;.&nbsp; | &nbsp;&nbsp;.&nbsp; | &nbsp;&nbsp;1&nbsp; | &nbsp;&nbsp;.&nbsp; | &nbsp;&nbsp;.&nbsp; | &nbsp;&nbsp;.&nbsp; | &nbsp;&nbsp;.&nbsp; | &nbsp;&nbsp;.&nbsp; | &nbsp;&nbsp;.&nbsp; | &nbsp;&nbsp;.&nbsp; | &nbsp;&nbsp;.&nbsp; | &nbsp;&nbsp;.&nbsp; | &nbsp;&nbsp;.&nbsp; | &nbsp;&nbsp;.&nbsp; | &nbsp;&nbsp;.&nbsp; | &nbsp;&nbsp;.&nbsp; | &nbsp;&nbsp;.&nbsp; |  &nbsp;&nbsp;1&nbsp; | &nbsp;&nbsp; Extrusion E2040 x 70mm |
| &nbsp;&nbsp;.&nbsp; | &nbsp;&nbsp;.&nbsp; | &nbsp;&nbsp;.&nbsp; | &nbsp;&nbsp;.&nbsp; | &nbsp;&nbsp;.&nbsp; | &nbsp;&nbsp;.&nbsp; | &nbsp;&nbsp;.&nbsp; | &nbsp;&nbsp;.&nbsp; | &nbsp;&nbsp;.&nbsp; | &nbsp;&nbsp;.&nbsp; | &nbsp;&nbsp;.&nbsp; | &nbsp;&nbsp;.&nbsp; | &nbsp;&nbsp;.&nbsp; | &nbsp;&nbsp;.&nbsp; | &nbsp;&nbsp;.&nbsp; | &nbsp;&nbsp;.&nbsp; | &nbsp;&nbsp;.&nbsp; | &nbsp;&nbsp;.&nbsp; | &nbsp;&nbsp;.&nbsp; | &nbsp;&nbsp;1&nbsp; | &nbsp;&nbsp;.&nbsp; | &nbsp;&nbsp;.&nbsp; |  &nbsp;&nbsp;1&nbsp; | &nbsp;&nbsp; Flat section 15mmx2mm, 272mm |
| &nbsp;&nbsp;.&nbsp; | &nbsp;&nbsp;.&nbsp; | &nbsp;&nbsp;.&nbsp; | &nbsp;&nbsp;.&nbsp; | &nbsp;&nbsp;.&nbsp; | &nbsp;&nbsp;.&nbsp; | &nbsp;&nbsp;.&nbsp; | &nbsp;&nbsp;.&nbsp; | &nbsp;&nbsp;.&nbsp; | &nbsp;&nbsp;.&nbsp; | &nbsp;&nbsp;.&nbsp; | &nbsp;&nbsp;.&nbsp; | &nbsp;&nbsp;.&nbsp; | &nbsp;&nbsp;.&nbsp; | &nbsp;&nbsp;.&nbsp; | &nbsp;&nbsp;.&nbsp; | &nbsp;&nbsp;.&nbsp; | &nbsp;&nbsp;.&nbsp; | &nbsp;&nbsp;.&nbsp; | &nbsp;&nbsp;4&nbsp; | &nbsp;&nbsp;.&nbsp; | &nbsp;&nbsp;.&nbsp; |  &nbsp;&nbsp;4&nbsp; | &nbsp;&nbsp; Flat section 15mmx2mm, 316mm |
| &nbsp;&nbsp;.&nbsp; | &nbsp;&nbsp;.&nbsp; | &nbsp;&nbsp;.&nbsp; | &nbsp;&nbsp;.&nbsp; | &nbsp;&nbsp;.&nbsp; | &nbsp;&nbsp;.&nbsp; | &nbsp;&nbsp;.&nbsp; | &nbsp;&nbsp;2&nbsp; | &nbsp;&nbsp;.&nbsp; | &nbsp;&nbsp;.&nbsp; | &nbsp;&nbsp;2&nbsp; | &nbsp;&nbsp;.&nbsp; | &nbsp;&nbsp;.&nbsp; | &nbsp;&nbsp;.&nbsp; | &nbsp;&nbsp;4&nbsp; | &nbsp;&nbsp;.&nbsp; | &nbsp;&nbsp;.&nbsp; | &nbsp;&nbsp;.&nbsp; | &nbsp;&nbsp;.&nbsp; | &nbsp;&nbsp;.&nbsp; | &nbsp;&nbsp;.&nbsp; | &nbsp;&nbsp;.&nbsp; |  &nbsp;&nbsp;8&nbsp; | &nbsp;&nbsp; L-Bracket (20x20) |
| &nbsp;&nbsp;.&nbsp; | &nbsp;&nbsp;.&nbsp; | &nbsp;&nbsp;.&nbsp; | &nbsp;&nbsp;.&nbsp; | &nbsp;&nbsp;.&nbsp; | &nbsp;&nbsp;.&nbsp; | &nbsp;&nbsp;4&nbsp; | &nbsp;&nbsp;.&nbsp; | &nbsp;&nbsp;.&nbsp; | &nbsp;&nbsp;.&nbsp; | &nbsp;&nbsp;.&nbsp; | &nbsp;&nbsp;.&nbsp; | &nbsp;&nbsp;.&nbsp; | &nbsp;&nbsp;.&nbsp; | &nbsp;&nbsp;.&nbsp; | &nbsp;&nbsp;.&nbsp; | &nbsp;&nbsp;.&nbsp; | &nbsp;&nbsp;.&nbsp; | &nbsp;&nbsp;.&nbsp; | &nbsp;&nbsp;.&nbsp; | &nbsp;&nbsp;.&nbsp; | &nbsp;&nbsp;.&nbsp; |  &nbsp;&nbsp;4&nbsp; | &nbsp;&nbsp; Linear rail MGN7 x 70mm |
| &nbsp;&nbsp;.&nbsp; | &nbsp;&nbsp;1&nbsp; | &nbsp;&nbsp;1&nbsp; | &nbsp;&nbsp;.&nbsp; | &nbsp;&nbsp;1&nbsp; | &nbsp;&nbsp;1&nbsp; | &nbsp;&nbsp;.&nbsp; | &nbsp;&nbsp;.&nbsp; | &nbsp;&nbsp;.&nbsp; | &nbsp;&nbsp;.&nbsp; | &nbsp;&nbsp;.&nbsp; | &nbsp;&nbsp;.&nbsp; | &nbsp;&nbsp;.&nbsp; | &nbsp;&nbsp;.&nbsp; | &nbsp;&nbsp;.&nbsp; | &nbsp;&nbsp;.&nbsp; | &nbsp;&nbsp;.&nbsp; | &nbsp;&nbsp;.&nbsp; | &nbsp;&nbsp;.&nbsp; | &nbsp;&nbsp;.&nbsp; | &nbsp;&nbsp;.&nbsp; | &nbsp;&nbsp;.&nbsp; |  &nbsp;&nbsp;4&nbsp; | &nbsp;&nbsp; Linear rail carriage MGN7C |
| &nbsp;&nbsp;.&nbsp; | &nbsp;&nbsp;.&nbsp; | &nbsp;&nbsp;.&nbsp; | &nbsp;&nbsp;.&nbsp; | &nbsp;&nbsp;.&nbsp; | &nbsp;&nbsp;.&nbsp; | &nbsp;&nbsp;.&nbsp; | &nbsp;&nbsp;.&nbsp; | &nbsp;&nbsp;.&nbsp; | &nbsp;&nbsp;.&nbsp; | &nbsp;&nbsp;.&nbsp; | &nbsp;&nbsp;.&nbsp; | &nbsp;&nbsp;4&nbsp; | &nbsp;&nbsp;.&nbsp; | &nbsp;&nbsp;.&nbsp; | &nbsp;&nbsp;.&nbsp; | &nbsp;&nbsp;.&nbsp; | &nbsp;&nbsp;.&nbsp; | &nbsp;&nbsp;.&nbsp; | &nbsp;&nbsp;.&nbsp; | &nbsp;&nbsp;.&nbsp; | &nbsp;&nbsp;.&nbsp; |  &nbsp;&nbsp;4&nbsp; | &nbsp;&nbsp; Neodym Magnet (D=20,H=4.5) |
| &nbsp;&nbsp;.&nbsp; | &nbsp;&nbsp;.&nbsp; | &nbsp;&nbsp;.&nbsp; | &nbsp;&nbsp;.&nbsp; | &nbsp;&nbsp;.&nbsp; | &nbsp;&nbsp;.&nbsp; | &nbsp;&nbsp;20&nbsp; | &nbsp;&nbsp;.&nbsp; | &nbsp;&nbsp;.&nbsp; | &nbsp;&nbsp;.&nbsp; | &nbsp;&nbsp;.&nbsp; | &nbsp;&nbsp;.&nbsp; | &nbsp;&nbsp;.&nbsp; | &nbsp;&nbsp;.&nbsp; | &nbsp;&nbsp;.&nbsp; | &nbsp;&nbsp;.&nbsp; | &nbsp;&nbsp;.&nbsp; | &nbsp;&nbsp;.&nbsp; | &nbsp;&nbsp;.&nbsp; | &nbsp;&nbsp;.&nbsp; | &nbsp;&nbsp;.&nbsp; | &nbsp;&nbsp;.&nbsp; |  &nbsp;&nbsp;20&nbsp; | &nbsp;&nbsp; Nut M2 x 1.6mm  |
| &nbsp;&nbsp;.&nbsp; | &nbsp;&nbsp;2&nbsp; | &nbsp;&nbsp;2&nbsp; | &nbsp;&nbsp;.&nbsp; | &nbsp;&nbsp;2&nbsp; | &nbsp;&nbsp;2&nbsp; | &nbsp;&nbsp;.&nbsp; | &nbsp;&nbsp;.&nbsp; | &nbsp;&nbsp;.&nbsp; | &nbsp;&nbsp;.&nbsp; | &nbsp;&nbsp;.&nbsp; | &nbsp;&nbsp;.&nbsp; | &nbsp;&nbsp;.&nbsp; | &nbsp;&nbsp;.&nbsp; | &nbsp;&nbsp;.&nbsp; | &nbsp;&nbsp;.&nbsp; | &nbsp;&nbsp;.&nbsp; | &nbsp;&nbsp;.&nbsp; | &nbsp;&nbsp;.&nbsp; | &nbsp;&nbsp;.&nbsp; | &nbsp;&nbsp;.&nbsp; | &nbsp;&nbsp;.&nbsp; |  &nbsp;&nbsp;8&nbsp; | &nbsp;&nbsp; Nut M3 x 2.4mm  |
| &nbsp;&nbsp;.&nbsp; | &nbsp;&nbsp;.&nbsp; | &nbsp;&nbsp;.&nbsp; | &nbsp;&nbsp;.&nbsp; | &nbsp;&nbsp;.&nbsp; | &nbsp;&nbsp;.&nbsp; | &nbsp;&nbsp;.&nbsp; | &nbsp;&nbsp;.&nbsp; | &nbsp;&nbsp;1&nbsp; | &nbsp;&nbsp;.&nbsp; | &nbsp;&nbsp;.&nbsp; | &nbsp;&nbsp;.&nbsp; | &nbsp;&nbsp;.&nbsp; | &nbsp;&nbsp;.&nbsp; | &nbsp;&nbsp;.&nbsp; | &nbsp;&nbsp;.&nbsp; | &nbsp;&nbsp;.&nbsp; | &nbsp;&nbsp;.&nbsp; | &nbsp;&nbsp;.&nbsp; | &nbsp;&nbsp;.&nbsp; | &nbsp;&nbsp;.&nbsp; | &nbsp;&nbsp;.&nbsp; |  &nbsp;&nbsp;1&nbsp; | &nbsp;&nbsp; Nut M5 x 4mm  |
| &nbsp;&nbsp;.&nbsp; | &nbsp;&nbsp;.&nbsp; | &nbsp;&nbsp;.&nbsp; | &nbsp;&nbsp;.&nbsp; | &nbsp;&nbsp;.&nbsp; | &nbsp;&nbsp;.&nbsp; | &nbsp;&nbsp;.&nbsp; | &nbsp;&nbsp;1&nbsp; | &nbsp;&nbsp;.&nbsp; | &nbsp;&nbsp;.&nbsp; | &nbsp;&nbsp;.&nbsp; | &nbsp;&nbsp;.&nbsp; | &nbsp;&nbsp;.&nbsp; | &nbsp;&nbsp;.&nbsp; | &nbsp;&nbsp;.&nbsp; | &nbsp;&nbsp;.&nbsp; | &nbsp;&nbsp;.&nbsp; | &nbsp;&nbsp;.&nbsp; | &nbsp;&nbsp;.&nbsp; | &nbsp;&nbsp;.&nbsp; | &nbsp;&nbsp;.&nbsp; | &nbsp;&nbsp;.&nbsp; |  &nbsp;&nbsp;1&nbsp; | &nbsp;&nbsp; Nut M8 x 6.5mm  |
| &nbsp;&nbsp;.&nbsp; | &nbsp;&nbsp;.&nbsp; | &nbsp;&nbsp;.&nbsp; | &nbsp;&nbsp;.&nbsp; | &nbsp;&nbsp;.&nbsp; | &nbsp;&nbsp;.&nbsp; | &nbsp;&nbsp;.&nbsp; | &nbsp;&nbsp;.&nbsp; | &nbsp;&nbsp;1&nbsp; | &nbsp;&nbsp;.&nbsp; | &nbsp;&nbsp;.&nbsp; | &nbsp;&nbsp;.&nbsp; | &nbsp;&nbsp;.&nbsp; | &nbsp;&nbsp;.&nbsp; | &nbsp;&nbsp;.&nbsp; | &nbsp;&nbsp;.&nbsp; | &nbsp;&nbsp;.&nbsp; | &nbsp;&nbsp;.&nbsp; | &nbsp;&nbsp;.&nbsp; | &nbsp;&nbsp;.&nbsp; | &nbsp;&nbsp;.&nbsp; | &nbsp;&nbsp;.&nbsp; |  &nbsp;&nbsp;1&nbsp; | &nbsp;&nbsp; Pulley GT2 idler 20 teeth |
| &nbsp;&nbsp;.&nbsp; | &nbsp;&nbsp;.&nbsp; | &nbsp;&nbsp;.&nbsp; | &nbsp;&nbsp;.&nbsp; | &nbsp;&nbsp;.&nbsp; | &nbsp;&nbsp;.&nbsp; | &nbsp;&nbsp;.&nbsp; | &nbsp;&nbsp;2&nbsp; | &nbsp;&nbsp;.&nbsp; | &nbsp;&nbsp;.&nbsp; | &nbsp;&nbsp;.&nbsp; | &nbsp;&nbsp;.&nbsp; | &nbsp;&nbsp;.&nbsp; | &nbsp;&nbsp;.&nbsp; | &nbsp;&nbsp;.&nbsp; | &nbsp;&nbsp;.&nbsp; | &nbsp;&nbsp;.&nbsp; | &nbsp;&nbsp;.&nbsp; | &nbsp;&nbsp;.&nbsp; | &nbsp;&nbsp;.&nbsp; | &nbsp;&nbsp;.&nbsp; | &nbsp;&nbsp;.&nbsp; |  &nbsp;&nbsp;2&nbsp; | &nbsp;&nbsp; Pulley GT2 idler smooth 12mm |
| &nbsp;&nbsp;.&nbsp; | &nbsp;&nbsp;.&nbsp; | &nbsp;&nbsp;.&nbsp; | &nbsp;&nbsp;.&nbsp; | &nbsp;&nbsp;.&nbsp; | &nbsp;&nbsp;.&nbsp; | &nbsp;&nbsp;.&nbsp; | &nbsp;&nbsp;1&nbsp; | &nbsp;&nbsp;.&nbsp; | &nbsp;&nbsp;4&nbsp; | &nbsp;&nbsp;.&nbsp; | &nbsp;&nbsp;.&nbsp; | &nbsp;&nbsp;.&nbsp; | &nbsp;&nbsp;.&nbsp; | &nbsp;&nbsp;.&nbsp; | &nbsp;&nbsp;.&nbsp; | &nbsp;&nbsp;.&nbsp; | &nbsp;&nbsp;.&nbsp; | &nbsp;&nbsp;.&nbsp; | &nbsp;&nbsp;.&nbsp; | &nbsp;&nbsp;.&nbsp; | &nbsp;&nbsp;.&nbsp; |  &nbsp;&nbsp;5&nbsp; | &nbsp;&nbsp; Pulley GT2OB 20 teeth |
| &nbsp;&nbsp;.&nbsp; | &nbsp;&nbsp;.&nbsp; | &nbsp;&nbsp;.&nbsp; | &nbsp;&nbsp;.&nbsp; | &nbsp;&nbsp;.&nbsp; | &nbsp;&nbsp;.&nbsp; | &nbsp;&nbsp;20&nbsp; | &nbsp;&nbsp;.&nbsp; | &nbsp;&nbsp;.&nbsp; | &nbsp;&nbsp;.&nbsp; | &nbsp;&nbsp;.&nbsp; | &nbsp;&nbsp;.&nbsp; | &nbsp;&nbsp;.&nbsp; | &nbsp;&nbsp;.&nbsp; | &nbsp;&nbsp;.&nbsp; | &nbsp;&nbsp;.&nbsp; | &nbsp;&nbsp;.&nbsp; | &nbsp;&nbsp;.&nbsp; | &nbsp;&nbsp;.&nbsp; | &nbsp;&nbsp;.&nbsp; | &nbsp;&nbsp;.&nbsp; | &nbsp;&nbsp;.&nbsp; |  &nbsp;&nbsp;20&nbsp; | &nbsp;&nbsp; Screw M2 cap x  6mm |
| &nbsp;&nbsp;.&nbsp; | &nbsp;&nbsp;4&nbsp; | &nbsp;&nbsp;4&nbsp; | &nbsp;&nbsp;.&nbsp; | &nbsp;&nbsp;4&nbsp; | &nbsp;&nbsp;4&nbsp; | &nbsp;&nbsp;.&nbsp; | &nbsp;&nbsp;.&nbsp; | &nbsp;&nbsp;.&nbsp; | &nbsp;&nbsp;.&nbsp; | &nbsp;&nbsp;.&nbsp; | &nbsp;&nbsp;.&nbsp; | &nbsp;&nbsp;.&nbsp; | &nbsp;&nbsp;.&nbsp; | &nbsp;&nbsp;.&nbsp; | &nbsp;&nbsp;.&nbsp; | &nbsp;&nbsp;.&nbsp; | &nbsp;&nbsp;.&nbsp; | &nbsp;&nbsp;.&nbsp; | &nbsp;&nbsp;.&nbsp; | &nbsp;&nbsp;.&nbsp; | &nbsp;&nbsp;.&nbsp; |  &nbsp;&nbsp;16&nbsp; | &nbsp;&nbsp; Screw M2 cap x 10mm |
| &nbsp;&nbsp;.&nbsp; | &nbsp;&nbsp;.&nbsp; | &nbsp;&nbsp;.&nbsp; | &nbsp;&nbsp;.&nbsp; | &nbsp;&nbsp;.&nbsp; | &nbsp;&nbsp;.&nbsp; | &nbsp;&nbsp;.&nbsp; | &nbsp;&nbsp;6&nbsp; | &nbsp;&nbsp;.&nbsp; | &nbsp;&nbsp;8&nbsp; | &nbsp;&nbsp;4&nbsp; | &nbsp;&nbsp;.&nbsp; | &nbsp;&nbsp;.&nbsp; | &nbsp;&nbsp;.&nbsp; | &nbsp;&nbsp;8&nbsp; | &nbsp;&nbsp;.&nbsp; | &nbsp;&nbsp;.&nbsp; | &nbsp;&nbsp;.&nbsp; | &nbsp;&nbsp;.&nbsp; | &nbsp;&nbsp;.&nbsp; | &nbsp;&nbsp;.&nbsp; | &nbsp;&nbsp;.&nbsp; |  &nbsp;&nbsp;26&nbsp; | &nbsp;&nbsp; Screw M3 grub x  6mm |
| &nbsp;&nbsp;.&nbsp; | &nbsp;&nbsp;2&nbsp; | &nbsp;&nbsp;2&nbsp; | &nbsp;&nbsp;.&nbsp; | &nbsp;&nbsp;2&nbsp; | &nbsp;&nbsp;2&nbsp; | &nbsp;&nbsp;.&nbsp; | &nbsp;&nbsp;.&nbsp; | &nbsp;&nbsp;.&nbsp; | &nbsp;&nbsp;.&nbsp; | &nbsp;&nbsp;.&nbsp; | &nbsp;&nbsp;.&nbsp; | &nbsp;&nbsp;.&nbsp; | &nbsp;&nbsp;.&nbsp; | &nbsp;&nbsp;.&nbsp; | &nbsp;&nbsp;.&nbsp; | &nbsp;&nbsp;.&nbsp; | &nbsp;&nbsp;.&nbsp; | &nbsp;&nbsp;.&nbsp; | &nbsp;&nbsp;.&nbsp; | &nbsp;&nbsp;.&nbsp; | &nbsp;&nbsp;.&nbsp; |  &nbsp;&nbsp;8&nbsp; | &nbsp;&nbsp; Screw M3 pan x 12mm |
| &nbsp;&nbsp;.&nbsp; | &nbsp;&nbsp;1&nbsp; | &nbsp;&nbsp;1&nbsp; | &nbsp;&nbsp;.&nbsp; | &nbsp;&nbsp;1&nbsp; | &nbsp;&nbsp;1&nbsp; | &nbsp;&nbsp;.&nbsp; | &nbsp;&nbsp;.&nbsp; | &nbsp;&nbsp;2&nbsp; | &nbsp;&nbsp;8&nbsp; | &nbsp;&nbsp;.&nbsp; | &nbsp;&nbsp;.&nbsp; | &nbsp;&nbsp;8&nbsp; | &nbsp;&nbsp;.&nbsp; | &nbsp;&nbsp;.&nbsp; | &nbsp;&nbsp;.&nbsp; | &nbsp;&nbsp;.&nbsp; | &nbsp;&nbsp;.&nbsp; | &nbsp;&nbsp;.&nbsp; | &nbsp;&nbsp;.&nbsp; | &nbsp;&nbsp;.&nbsp; | &nbsp;&nbsp;.&nbsp; |  &nbsp;&nbsp;22&nbsp; | &nbsp;&nbsp; Screw M4 cap x 12mm |
| &nbsp;&nbsp;.&nbsp; | &nbsp;&nbsp;.&nbsp; | &nbsp;&nbsp;.&nbsp; | &nbsp;&nbsp;.&nbsp; | &nbsp;&nbsp;.&nbsp; | &nbsp;&nbsp;.&nbsp; | &nbsp;&nbsp;.&nbsp; | &nbsp;&nbsp;2&nbsp; | &nbsp;&nbsp;.&nbsp; | &nbsp;&nbsp;.&nbsp; | &nbsp;&nbsp;.&nbsp; | &nbsp;&nbsp;.&nbsp; | &nbsp;&nbsp;.&nbsp; | &nbsp;&nbsp;.&nbsp; | &nbsp;&nbsp;.&nbsp; | &nbsp;&nbsp;.&nbsp; | &nbsp;&nbsp;.&nbsp; | &nbsp;&nbsp;.&nbsp; | &nbsp;&nbsp;.&nbsp; | &nbsp;&nbsp;.&nbsp; | &nbsp;&nbsp;.&nbsp; | &nbsp;&nbsp;.&nbsp; |  &nbsp;&nbsp;2&nbsp; | &nbsp;&nbsp; Screw M4 cap x 15mm |
| &nbsp;&nbsp;.&nbsp; | &nbsp;&nbsp;.&nbsp; | &nbsp;&nbsp;.&nbsp; | &nbsp;&nbsp;.&nbsp; | &nbsp;&nbsp;.&nbsp; | &nbsp;&nbsp;.&nbsp; | &nbsp;&nbsp;.&nbsp; | &nbsp;&nbsp;4&nbsp; | &nbsp;&nbsp;.&nbsp; | &nbsp;&nbsp;.&nbsp; | &nbsp;&nbsp;.&nbsp; | &nbsp;&nbsp;.&nbsp; | &nbsp;&nbsp;.&nbsp; | &nbsp;&nbsp;.&nbsp; | &nbsp;&nbsp;.&nbsp; | &nbsp;&nbsp;.&nbsp; | &nbsp;&nbsp;.&nbsp; | &nbsp;&nbsp;.&nbsp; | &nbsp;&nbsp;.&nbsp; | &nbsp;&nbsp;.&nbsp; | &nbsp;&nbsp;.&nbsp; | &nbsp;&nbsp;.&nbsp; |  &nbsp;&nbsp;4&nbsp; | &nbsp;&nbsp; Screw M4 dome x  8mm |
| &nbsp;&nbsp;.&nbsp; | &nbsp;&nbsp;.&nbsp; | &nbsp;&nbsp;.&nbsp; | &nbsp;&nbsp;.&nbsp; | &nbsp;&nbsp;.&nbsp; | &nbsp;&nbsp;.&nbsp; | &nbsp;&nbsp;.&nbsp; | &nbsp;&nbsp;.&nbsp; | &nbsp;&nbsp;1&nbsp; | &nbsp;&nbsp;.&nbsp; | &nbsp;&nbsp;.&nbsp; | &nbsp;&nbsp;.&nbsp; | &nbsp;&nbsp;.&nbsp; | &nbsp;&nbsp;.&nbsp; | &nbsp;&nbsp;.&nbsp; | &nbsp;&nbsp;.&nbsp; | &nbsp;&nbsp;.&nbsp; | &nbsp;&nbsp;.&nbsp; | &nbsp;&nbsp;.&nbsp; | &nbsp;&nbsp;.&nbsp; | &nbsp;&nbsp;.&nbsp; | &nbsp;&nbsp;.&nbsp; |  &nbsp;&nbsp;1&nbsp; | &nbsp;&nbsp; Screw M5 cap x 28mm |
| &nbsp;&nbsp;4&nbsp; | &nbsp;&nbsp;.&nbsp; | &nbsp;&nbsp;.&nbsp; | &nbsp;&nbsp;.&nbsp; | &nbsp;&nbsp;.&nbsp; | &nbsp;&nbsp;.&nbsp; | &nbsp;&nbsp;.&nbsp; | &nbsp;&nbsp;.&nbsp; | &nbsp;&nbsp;.&nbsp; | &nbsp;&nbsp;.&nbsp; | &nbsp;&nbsp;.&nbsp; | &nbsp;&nbsp;.&nbsp; | &nbsp;&nbsp;.&nbsp; | &nbsp;&nbsp;.&nbsp; | &nbsp;&nbsp;.&nbsp; | &nbsp;&nbsp;.&nbsp; | &nbsp;&nbsp;.&nbsp; | &nbsp;&nbsp;.&nbsp; | &nbsp;&nbsp;.&nbsp; | &nbsp;&nbsp;.&nbsp; | &nbsp;&nbsp;.&nbsp; | &nbsp;&nbsp;.&nbsp; |  &nbsp;&nbsp;4&nbsp; | &nbsp;&nbsp; Screw M6 cap x 20mm |
| &nbsp;&nbsp;.&nbsp; | &nbsp;&nbsp;1&nbsp; | &nbsp;&nbsp;1&nbsp; | &nbsp;&nbsp;.&nbsp; | &nbsp;&nbsp;1&nbsp; | &nbsp;&nbsp;1&nbsp; | &nbsp;&nbsp;.&nbsp; | &nbsp;&nbsp;.&nbsp; | &nbsp;&nbsp;.&nbsp; | &nbsp;&nbsp;.&nbsp; | &nbsp;&nbsp;.&nbsp; | &nbsp;&nbsp;.&nbsp; | &nbsp;&nbsp;.&nbsp; | &nbsp;&nbsp;.&nbsp; | &nbsp;&nbsp;.&nbsp; | &nbsp;&nbsp;.&nbsp; | &nbsp;&nbsp;.&nbsp; | &nbsp;&nbsp;.&nbsp; | &nbsp;&nbsp;.&nbsp; | &nbsp;&nbsp;.&nbsp; | &nbsp;&nbsp;.&nbsp; | &nbsp;&nbsp;.&nbsp; |  &nbsp;&nbsp;4&nbsp; | &nbsp;&nbsp; Screw M6 pan x 20mm |
| &nbsp;&nbsp;.&nbsp; | &nbsp;&nbsp;.&nbsp; | &nbsp;&nbsp;.&nbsp; | &nbsp;&nbsp;.&nbsp; | &nbsp;&nbsp;.&nbsp; | &nbsp;&nbsp;.&nbsp; | &nbsp;&nbsp;.&nbsp; | &nbsp;&nbsp;3&nbsp; | &nbsp;&nbsp;.&nbsp; | &nbsp;&nbsp;.&nbsp; | &nbsp;&nbsp;.&nbsp; | &nbsp;&nbsp;.&nbsp; | &nbsp;&nbsp;.&nbsp; | &nbsp;&nbsp;.&nbsp; | &nbsp;&nbsp;.&nbsp; | &nbsp;&nbsp;.&nbsp; | &nbsp;&nbsp;.&nbsp; | &nbsp;&nbsp;.&nbsp; | &nbsp;&nbsp;.&nbsp; | &nbsp;&nbsp;.&nbsp; | &nbsp;&nbsp;.&nbsp; | &nbsp;&nbsp;.&nbsp; |  &nbsp;&nbsp;3&nbsp; | &nbsp;&nbsp; Screw M8 hex x 50mm |
| &nbsp;&nbsp;.&nbsp; | &nbsp;&nbsp;1&nbsp; | &nbsp;&nbsp;1&nbsp; | &nbsp;&nbsp;.&nbsp; | &nbsp;&nbsp;1&nbsp; | &nbsp;&nbsp;1&nbsp; | &nbsp;&nbsp;.&nbsp; | &nbsp;&nbsp;.&nbsp; | &nbsp;&nbsp;2&nbsp; | &nbsp;&nbsp;8&nbsp; | &nbsp;&nbsp;.&nbsp; | &nbsp;&nbsp;.&nbsp; | &nbsp;&nbsp;8&nbsp; | &nbsp;&nbsp;.&nbsp; | &nbsp;&nbsp;.&nbsp; | &nbsp;&nbsp;.&nbsp; | &nbsp;&nbsp;.&nbsp; | &nbsp;&nbsp;.&nbsp; | &nbsp;&nbsp;.&nbsp; | &nbsp;&nbsp;.&nbsp; | &nbsp;&nbsp;.&nbsp; | &nbsp;&nbsp;.&nbsp; |  &nbsp;&nbsp;22&nbsp; | &nbsp;&nbsp; T-Nut (20x20) |
| &nbsp;&nbsp;.&nbsp; | &nbsp;&nbsp;.&nbsp; | &nbsp;&nbsp;.&nbsp; | &nbsp;&nbsp;.&nbsp; | &nbsp;&nbsp;.&nbsp; | &nbsp;&nbsp;.&nbsp; | &nbsp;&nbsp;.&nbsp; | &nbsp;&nbsp;4&nbsp; | &nbsp;&nbsp;.&nbsp; | &nbsp;&nbsp;.&nbsp; | &nbsp;&nbsp;.&nbsp; | &nbsp;&nbsp;.&nbsp; | &nbsp;&nbsp;.&nbsp; | &nbsp;&nbsp;.&nbsp; | &nbsp;&nbsp;.&nbsp; | &nbsp;&nbsp;.&nbsp; | &nbsp;&nbsp;.&nbsp; | &nbsp;&nbsp;.&nbsp; | &nbsp;&nbsp;.&nbsp; | &nbsp;&nbsp;.&nbsp; | &nbsp;&nbsp;.&nbsp; | &nbsp;&nbsp;.&nbsp; |  &nbsp;&nbsp;4&nbsp; | &nbsp;&nbsp; T-Nut (20x20) |
| &nbsp;&nbsp;.&nbsp; | &nbsp;&nbsp;.&nbsp; | &nbsp;&nbsp;.&nbsp; | &nbsp;&nbsp;.&nbsp; | &nbsp;&nbsp;.&nbsp; | &nbsp;&nbsp;.&nbsp; | &nbsp;&nbsp;.&nbsp; | &nbsp;&nbsp;2&nbsp; | &nbsp;&nbsp;.&nbsp; | &nbsp;&nbsp;.&nbsp; | &nbsp;&nbsp;.&nbsp; | &nbsp;&nbsp;.&nbsp; | &nbsp;&nbsp;.&nbsp; | &nbsp;&nbsp;.&nbsp; | &nbsp;&nbsp;.&nbsp; | &nbsp;&nbsp;.&nbsp; | &nbsp;&nbsp;.&nbsp; | &nbsp;&nbsp;.&nbsp; | &nbsp;&nbsp;.&nbsp; | &nbsp;&nbsp;.&nbsp; | &nbsp;&nbsp;.&nbsp; | &nbsp;&nbsp;.&nbsp; |  &nbsp;&nbsp;2&nbsp; | &nbsp;&nbsp; T-Nut (20x20) |
| &nbsp;&nbsp;.&nbsp; | &nbsp;&nbsp;1&nbsp; | &nbsp;&nbsp;1&nbsp; | &nbsp;&nbsp;.&nbsp; | &nbsp;&nbsp;1&nbsp; | &nbsp;&nbsp;1&nbsp; | &nbsp;&nbsp;.&nbsp; | &nbsp;&nbsp;.&nbsp; | &nbsp;&nbsp;.&nbsp; | &nbsp;&nbsp;.&nbsp; | &nbsp;&nbsp;.&nbsp; | &nbsp;&nbsp;.&nbsp; | &nbsp;&nbsp;.&nbsp; | &nbsp;&nbsp;.&nbsp; | &nbsp;&nbsp;.&nbsp; | &nbsp;&nbsp;.&nbsp; | &nbsp;&nbsp;.&nbsp; | &nbsp;&nbsp;.&nbsp; | &nbsp;&nbsp;.&nbsp; | &nbsp;&nbsp;.&nbsp; | &nbsp;&nbsp;.&nbsp; | &nbsp;&nbsp;.&nbsp; |  &nbsp;&nbsp;4&nbsp; | &nbsp;&nbsp; T8-Nut (narrow) |
| &nbsp;&nbsp;.&nbsp; | &nbsp;&nbsp;.&nbsp; | &nbsp;&nbsp;.&nbsp; | &nbsp;&nbsp;.&nbsp; | &nbsp;&nbsp;.&nbsp; | &nbsp;&nbsp;.&nbsp; | &nbsp;&nbsp;.&nbsp; | &nbsp;&nbsp;.&nbsp; | &nbsp;&nbsp;.&nbsp; | &nbsp;&nbsp;4&nbsp; | &nbsp;&nbsp;.&nbsp; | &nbsp;&nbsp;.&nbsp; | &nbsp;&nbsp;.&nbsp; | &nbsp;&nbsp;.&nbsp; | &nbsp;&nbsp;.&nbsp; | &nbsp;&nbsp;.&nbsp; | &nbsp;&nbsp;.&nbsp; | &nbsp;&nbsp;.&nbsp; | &nbsp;&nbsp;.&nbsp; | &nbsp;&nbsp;.&nbsp; | &nbsp;&nbsp;.&nbsp; | &nbsp;&nbsp;.&nbsp; |  &nbsp;&nbsp;4&nbsp; | &nbsp;&nbsp; Threaded rod M8 x 100mm |
| &nbsp;&nbsp;.&nbsp; | &nbsp;&nbsp;4&nbsp; | &nbsp;&nbsp;4&nbsp; | &nbsp;&nbsp;.&nbsp; | &nbsp;&nbsp;4&nbsp; | &nbsp;&nbsp;4&nbsp; | &nbsp;&nbsp;.&nbsp; | &nbsp;&nbsp;.&nbsp; | &nbsp;&nbsp;.&nbsp; | &nbsp;&nbsp;.&nbsp; | &nbsp;&nbsp;.&nbsp; | &nbsp;&nbsp;.&nbsp; | &nbsp;&nbsp;.&nbsp; | &nbsp;&nbsp;.&nbsp; | &nbsp;&nbsp;.&nbsp; | &nbsp;&nbsp;.&nbsp; | &nbsp;&nbsp;.&nbsp; | &nbsp;&nbsp;.&nbsp; | &nbsp;&nbsp;.&nbsp; | &nbsp;&nbsp;.&nbsp; | &nbsp;&nbsp;.&nbsp; | &nbsp;&nbsp;.&nbsp; |  &nbsp;&nbsp;16&nbsp; | &nbsp;&nbsp; Washer  M2 x 5mm x 0.3mm |
| &nbsp;&nbsp;.&nbsp; | &nbsp;&nbsp;1&nbsp; | &nbsp;&nbsp;1&nbsp; | &nbsp;&nbsp;.&nbsp; | &nbsp;&nbsp;1&nbsp; | &nbsp;&nbsp;1&nbsp; | &nbsp;&nbsp;.&nbsp; | &nbsp;&nbsp;6&nbsp; | &nbsp;&nbsp;2&nbsp; | &nbsp;&nbsp;8&nbsp; | &nbsp;&nbsp;.&nbsp; | &nbsp;&nbsp;.&nbsp; | &nbsp;&nbsp;8&nbsp; | &nbsp;&nbsp;.&nbsp; | &nbsp;&nbsp;.&nbsp; | &nbsp;&nbsp;.&nbsp; | &nbsp;&nbsp;.&nbsp; | &nbsp;&nbsp;.&nbsp; | &nbsp;&nbsp;.&nbsp; | &nbsp;&nbsp;.&nbsp; | &nbsp;&nbsp;.&nbsp; | &nbsp;&nbsp;.&nbsp; |  &nbsp;&nbsp;28&nbsp; | &nbsp;&nbsp; Washer  M4 x 9mm x 0.8mm |
| &nbsp;&nbsp;.&nbsp; | &nbsp;&nbsp;.&nbsp; | &nbsp;&nbsp;.&nbsp; | &nbsp;&nbsp;.&nbsp; | &nbsp;&nbsp;.&nbsp; | &nbsp;&nbsp;.&nbsp; | &nbsp;&nbsp;.&nbsp; | &nbsp;&nbsp;.&nbsp; | &nbsp;&nbsp;1&nbsp; | &nbsp;&nbsp;.&nbsp; | &nbsp;&nbsp;.&nbsp; | &nbsp;&nbsp;.&nbsp; | &nbsp;&nbsp;.&nbsp; | &nbsp;&nbsp;.&nbsp; | &nbsp;&nbsp;.&nbsp; | &nbsp;&nbsp;.&nbsp; | &nbsp;&nbsp;.&nbsp; | &nbsp;&nbsp;.&nbsp; | &nbsp;&nbsp;.&nbsp; | &nbsp;&nbsp;.&nbsp; | &nbsp;&nbsp;.&nbsp; | &nbsp;&nbsp;.&nbsp; |  &nbsp;&nbsp;1&nbsp; | &nbsp;&nbsp; Washer  M5 x 10mm x 1mm |
| &nbsp;&nbsp;4&nbsp; | &nbsp;&nbsp;1&nbsp; | &nbsp;&nbsp;1&nbsp; | &nbsp;&nbsp;.&nbsp; | &nbsp;&nbsp;1&nbsp; | &nbsp;&nbsp;1&nbsp; | &nbsp;&nbsp;.&nbsp; | &nbsp;&nbsp;.&nbsp; | &nbsp;&nbsp;.&nbsp; | &nbsp;&nbsp;.&nbsp; | &nbsp;&nbsp;.&nbsp; | &nbsp;&nbsp;.&nbsp; | &nbsp;&nbsp;.&nbsp; | &nbsp;&nbsp;.&nbsp; | &nbsp;&nbsp;.&nbsp; | &nbsp;&nbsp;.&nbsp; | &nbsp;&nbsp;.&nbsp; | &nbsp;&nbsp;.&nbsp; | &nbsp;&nbsp;.&nbsp; | &nbsp;&nbsp;.&nbsp; | &nbsp;&nbsp;.&nbsp; | &nbsp;&nbsp;.&nbsp; |  &nbsp;&nbsp;8&nbsp; | &nbsp;&nbsp; Washer  M6 x 12.5mm x 1.5mm |
| &nbsp;&nbsp;8&nbsp; | &nbsp;&nbsp;19&nbsp; | &nbsp;&nbsp;19&nbsp; | &nbsp;&nbsp;2&nbsp; | &nbsp;&nbsp;19&nbsp; | &nbsp;&nbsp;19&nbsp; | &nbsp;&nbsp;48&nbsp; | &nbsp;&nbsp;37&nbsp; | &nbsp;&nbsp;10&nbsp; | &nbsp;&nbsp;48&nbsp; | &nbsp;&nbsp;7&nbsp; | &nbsp;&nbsp;4&nbsp; | &nbsp;&nbsp;28&nbsp; | &nbsp;&nbsp;2&nbsp; | &nbsp;&nbsp;13&nbsp; | &nbsp;&nbsp;.&nbsp; | &nbsp;&nbsp;.&nbsp; | &nbsp;&nbsp;.&nbsp; | &nbsp;&nbsp;.&nbsp; | &nbsp;&nbsp;5&nbsp; | &nbsp;&nbsp;.&nbsp; | &nbsp;&nbsp;1&nbsp; | &nbsp;&nbsp;289&nbsp; | &nbsp;&nbsp;Total vitamins count |
|  |  |  |  |  |  |  |  |  |  |  |  |  |  |  |  |  |  |  |  |  |  | | **3D printed parts** |
| &nbsp;&nbsp;.&nbsp; | &nbsp;&nbsp;.&nbsp; | &nbsp;&nbsp;.&nbsp; | &nbsp;&nbsp;.&nbsp; | &nbsp;&nbsp;.&nbsp; | &nbsp;&nbsp;.&nbsp; | &nbsp;&nbsp;.&nbsp; | &nbsp;&nbsp;.&nbsp; | &nbsp;&nbsp;.&nbsp; | &nbsp;&nbsp;.&nbsp; | &nbsp;&nbsp;.&nbsp; | &nbsp;&nbsp;.&nbsp; | &nbsp;&nbsp;.&nbsp; | &nbsp;&nbsp;.&nbsp; | &nbsp;&nbsp;.&nbsp; | &nbsp;&nbsp;.&nbsp; | &nbsp;&nbsp;.&nbsp; | &nbsp;&nbsp;.&nbsp; | &nbsp;&nbsp;.&nbsp; | &nbsp;&nbsp;8&nbsp; | &nbsp;&nbsp;.&nbsp; | &nbsp;&nbsp;.&nbsp; |  &nbsp;&nbsp;8&nbsp; | &nbsp;&nbsp;DIYLB_beam_holder.stl |
| &nbsp;&nbsp;.&nbsp; | &nbsp;&nbsp;.&nbsp; | &nbsp;&nbsp;.&nbsp; | &nbsp;&nbsp;.&nbsp; | &nbsp;&nbsp;.&nbsp; | &nbsp;&nbsp;1&nbsp; | &nbsp;&nbsp;.&nbsp; | &nbsp;&nbsp;.&nbsp; | &nbsp;&nbsp;.&nbsp; | &nbsp;&nbsp;.&nbsp; | &nbsp;&nbsp;.&nbsp; | &nbsp;&nbsp;.&nbsp; | &nbsp;&nbsp;.&nbsp; | &nbsp;&nbsp;.&nbsp; | &nbsp;&nbsp;.&nbsp; | &nbsp;&nbsp;.&nbsp; | &nbsp;&nbsp;.&nbsp; | &nbsp;&nbsp;.&nbsp; | &nbsp;&nbsp;.&nbsp; | &nbsp;&nbsp;.&nbsp; | &nbsp;&nbsp;.&nbsp; | &nbsp;&nbsp;.&nbsp; |  &nbsp;&nbsp;1&nbsp; | &nbsp;&nbsp;DIYLB_carriage_A.stl |
| &nbsp;&nbsp;.&nbsp; | &nbsp;&nbsp;.&nbsp; | &nbsp;&nbsp;.&nbsp; | &nbsp;&nbsp;.&nbsp; | &nbsp;&nbsp;1&nbsp; | &nbsp;&nbsp;.&nbsp; | &nbsp;&nbsp;.&nbsp; | &nbsp;&nbsp;.&nbsp; | &nbsp;&nbsp;.&nbsp; | &nbsp;&nbsp;.&nbsp; | &nbsp;&nbsp;.&nbsp; | &nbsp;&nbsp;.&nbsp; | &nbsp;&nbsp;.&nbsp; | &nbsp;&nbsp;.&nbsp; | &nbsp;&nbsp;.&nbsp; | &nbsp;&nbsp;.&nbsp; | &nbsp;&nbsp;.&nbsp; | &nbsp;&nbsp;.&nbsp; | &nbsp;&nbsp;.&nbsp; | &nbsp;&nbsp;.&nbsp; | &nbsp;&nbsp;.&nbsp; | &nbsp;&nbsp;.&nbsp; |  &nbsp;&nbsp;1&nbsp; | &nbsp;&nbsp;DIYLB_carriage_B.stl |
| &nbsp;&nbsp;.&nbsp; | &nbsp;&nbsp;.&nbsp; | &nbsp;&nbsp;1&nbsp; | &nbsp;&nbsp;.&nbsp; | &nbsp;&nbsp;.&nbsp; | &nbsp;&nbsp;.&nbsp; | &nbsp;&nbsp;.&nbsp; | &nbsp;&nbsp;.&nbsp; | &nbsp;&nbsp;.&nbsp; | &nbsp;&nbsp;.&nbsp; | &nbsp;&nbsp;.&nbsp; | &nbsp;&nbsp;.&nbsp; | &nbsp;&nbsp;.&nbsp; | &nbsp;&nbsp;.&nbsp; | &nbsp;&nbsp;.&nbsp; | &nbsp;&nbsp;.&nbsp; | &nbsp;&nbsp;.&nbsp; | &nbsp;&nbsp;.&nbsp; | &nbsp;&nbsp;.&nbsp; | &nbsp;&nbsp;.&nbsp; | &nbsp;&nbsp;.&nbsp; | &nbsp;&nbsp;.&nbsp; |  &nbsp;&nbsp;1&nbsp; | &nbsp;&nbsp;DIYLB_carriage_C.stl |
| &nbsp;&nbsp;.&nbsp; | &nbsp;&nbsp;1&nbsp; | &nbsp;&nbsp;.&nbsp; | &nbsp;&nbsp;.&nbsp; | &nbsp;&nbsp;.&nbsp; | &nbsp;&nbsp;.&nbsp; | &nbsp;&nbsp;.&nbsp; | &nbsp;&nbsp;.&nbsp; | &nbsp;&nbsp;.&nbsp; | &nbsp;&nbsp;.&nbsp; | &nbsp;&nbsp;.&nbsp; | &nbsp;&nbsp;.&nbsp; | &nbsp;&nbsp;.&nbsp; | &nbsp;&nbsp;.&nbsp; | &nbsp;&nbsp;.&nbsp; | &nbsp;&nbsp;.&nbsp; | &nbsp;&nbsp;.&nbsp; | &nbsp;&nbsp;.&nbsp; | &nbsp;&nbsp;.&nbsp; | &nbsp;&nbsp;.&nbsp; | &nbsp;&nbsp;.&nbsp; | &nbsp;&nbsp;.&nbsp; |  &nbsp;&nbsp;1&nbsp; | &nbsp;&nbsp;DIYLB_carriage_D.stl |
| &nbsp;&nbsp;.&nbsp; | &nbsp;&nbsp;.&nbsp; | &nbsp;&nbsp;.&nbsp; | &nbsp;&nbsp;.&nbsp; | &nbsp;&nbsp;.&nbsp; | &nbsp;&nbsp;.&nbsp; | &nbsp;&nbsp;.&nbsp; | &nbsp;&nbsp;1&nbsp; | &nbsp;&nbsp;.&nbsp; | &nbsp;&nbsp;.&nbsp; | &nbsp;&nbsp;.&nbsp; | &nbsp;&nbsp;.&nbsp; | &nbsp;&nbsp;.&nbsp; | &nbsp;&nbsp;.&nbsp; | &nbsp;&nbsp;.&nbsp; | &nbsp;&nbsp;.&nbsp; | &nbsp;&nbsp;.&nbsp; | &nbsp;&nbsp;.&nbsp; | &nbsp;&nbsp;.&nbsp; | &nbsp;&nbsp;.&nbsp; | &nbsp;&nbsp;.&nbsp; | &nbsp;&nbsp;.&nbsp; |  &nbsp;&nbsp;1&nbsp; | &nbsp;&nbsp;DIYLB_crank.stl |
| &nbsp;&nbsp;.&nbsp; | &nbsp;&nbsp;.&nbsp; | &nbsp;&nbsp;.&nbsp; | &nbsp;&nbsp;.&nbsp; | &nbsp;&nbsp;.&nbsp; | &nbsp;&nbsp;.&nbsp; | &nbsp;&nbsp;.&nbsp; | &nbsp;&nbsp;2&nbsp; | &nbsp;&nbsp;.&nbsp; | &nbsp;&nbsp;.&nbsp; | &nbsp;&nbsp;.&nbsp; | &nbsp;&nbsp;.&nbsp; | &nbsp;&nbsp;.&nbsp; | &nbsp;&nbsp;.&nbsp; | &nbsp;&nbsp;.&nbsp; | &nbsp;&nbsp;.&nbsp; | &nbsp;&nbsp;.&nbsp; | &nbsp;&nbsp;.&nbsp; | &nbsp;&nbsp;.&nbsp; | &nbsp;&nbsp;.&nbsp; | &nbsp;&nbsp;.&nbsp; | &nbsp;&nbsp;.&nbsp; |  &nbsp;&nbsp;2&nbsp; | &nbsp;&nbsp;DIYLB_crank_bearing.stl |
| &nbsp;&nbsp;.&nbsp; | &nbsp;&nbsp;.&nbsp; | &nbsp;&nbsp;.&nbsp; | &nbsp;&nbsp;.&nbsp; | &nbsp;&nbsp;.&nbsp; | &nbsp;&nbsp;.&nbsp; | &nbsp;&nbsp;.&nbsp; | &nbsp;&nbsp;.&nbsp; | &nbsp;&nbsp;1&nbsp; | &nbsp;&nbsp;.&nbsp; | &nbsp;&nbsp;.&nbsp; | &nbsp;&nbsp;.&nbsp; | &nbsp;&nbsp;.&nbsp; | &nbsp;&nbsp;.&nbsp; | &nbsp;&nbsp;.&nbsp; | &nbsp;&nbsp;.&nbsp; | &nbsp;&nbsp;.&nbsp; | &nbsp;&nbsp;.&nbsp; | &nbsp;&nbsp;.&nbsp; | &nbsp;&nbsp;.&nbsp; | &nbsp;&nbsp;.&nbsp; | &nbsp;&nbsp;.&nbsp; |  &nbsp;&nbsp;1&nbsp; | &nbsp;&nbsp;DIYLB_idler.stl |
| &nbsp;&nbsp;.&nbsp; | &nbsp;&nbsp;.&nbsp; | &nbsp;&nbsp;.&nbsp; | &nbsp;&nbsp;.&nbsp; | &nbsp;&nbsp;.&nbsp; | &nbsp;&nbsp;.&nbsp; | &nbsp;&nbsp;.&nbsp; | &nbsp;&nbsp;.&nbsp; | &nbsp;&nbsp;.&nbsp; | &nbsp;&nbsp;4&nbsp; | &nbsp;&nbsp;.&nbsp; | &nbsp;&nbsp;.&nbsp; | &nbsp;&nbsp;.&nbsp; | &nbsp;&nbsp;.&nbsp; | &nbsp;&nbsp;.&nbsp; | &nbsp;&nbsp;.&nbsp; | &nbsp;&nbsp;.&nbsp; | &nbsp;&nbsp;.&nbsp; | &nbsp;&nbsp;.&nbsp; | &nbsp;&nbsp;.&nbsp; | &nbsp;&nbsp;.&nbsp; | &nbsp;&nbsp;.&nbsp; |  &nbsp;&nbsp;4&nbsp; | &nbsp;&nbsp;DIYLB_lower_bearing.stl |
| &nbsp;&nbsp;.&nbsp; | &nbsp;&nbsp;.&nbsp; | &nbsp;&nbsp;.&nbsp; | &nbsp;&nbsp;.&nbsp; | &nbsp;&nbsp;.&nbsp; | &nbsp;&nbsp;.&nbsp; | &nbsp;&nbsp;.&nbsp; | &nbsp;&nbsp;.&nbsp; | &nbsp;&nbsp;.&nbsp; | &nbsp;&nbsp;.&nbsp; | &nbsp;&nbsp;.&nbsp; | &nbsp;&nbsp;.&nbsp; | &nbsp;&nbsp;4&nbsp; | &nbsp;&nbsp;.&nbsp; | &nbsp;&nbsp;.&nbsp; | &nbsp;&nbsp;.&nbsp; | &nbsp;&nbsp;.&nbsp; | &nbsp;&nbsp;.&nbsp; | &nbsp;&nbsp;.&nbsp; | &nbsp;&nbsp;.&nbsp; | &nbsp;&nbsp;.&nbsp; | &nbsp;&nbsp;.&nbsp; |  &nbsp;&nbsp;4&nbsp; | &nbsp;&nbsp;DIYLB_magnet.stl |
| &nbsp;&nbsp;.&nbsp; | &nbsp;&nbsp;.&nbsp; | &nbsp;&nbsp;.&nbsp; | &nbsp;&nbsp;.&nbsp; | &nbsp;&nbsp;.&nbsp; | &nbsp;&nbsp;.&nbsp; | &nbsp;&nbsp;.&nbsp; | &nbsp;&nbsp;.&nbsp; | &nbsp;&nbsp;.&nbsp; | &nbsp;&nbsp;.&nbsp; | &nbsp;&nbsp;.&nbsp; | &nbsp;&nbsp;4&nbsp; | &nbsp;&nbsp;.&nbsp; | &nbsp;&nbsp;.&nbsp; | &nbsp;&nbsp;.&nbsp; | &nbsp;&nbsp;.&nbsp; | &nbsp;&nbsp;.&nbsp; | &nbsp;&nbsp;.&nbsp; | &nbsp;&nbsp;.&nbsp; | &nbsp;&nbsp;.&nbsp; | &nbsp;&nbsp;.&nbsp; | &nbsp;&nbsp;.&nbsp; |  &nbsp;&nbsp;4&nbsp; | &nbsp;&nbsp;DIYLB_magnet_cover.stl |
| &nbsp;&nbsp;.&nbsp; | &nbsp;&nbsp;.&nbsp; | &nbsp;&nbsp;.&nbsp; | &nbsp;&nbsp;.&nbsp; | &nbsp;&nbsp;.&nbsp; | &nbsp;&nbsp;.&nbsp; | &nbsp;&nbsp;4&nbsp; | &nbsp;&nbsp;.&nbsp; | &nbsp;&nbsp;.&nbsp; | &nbsp;&nbsp;.&nbsp; | &nbsp;&nbsp;.&nbsp; | &nbsp;&nbsp;.&nbsp; | &nbsp;&nbsp;.&nbsp; | &nbsp;&nbsp;.&nbsp; | &nbsp;&nbsp;.&nbsp; | &nbsp;&nbsp;.&nbsp; | &nbsp;&nbsp;.&nbsp; | &nbsp;&nbsp;.&nbsp; | &nbsp;&nbsp;.&nbsp; | &nbsp;&nbsp;.&nbsp; | &nbsp;&nbsp;.&nbsp; | &nbsp;&nbsp;.&nbsp; |  &nbsp;&nbsp;4&nbsp; | &nbsp;&nbsp;DIYLB_rail.stl |
| &nbsp;&nbsp;2&nbsp; | &nbsp;&nbsp;.&nbsp; | &nbsp;&nbsp;.&nbsp; | &nbsp;&nbsp;.&nbsp; | &nbsp;&nbsp;.&nbsp; | &nbsp;&nbsp;.&nbsp; | &nbsp;&nbsp;.&nbsp; | &nbsp;&nbsp;.&nbsp; | &nbsp;&nbsp;.&nbsp; | &nbsp;&nbsp;.&nbsp; | &nbsp;&nbsp;.&nbsp; | &nbsp;&nbsp;.&nbsp; | &nbsp;&nbsp;.&nbsp; | &nbsp;&nbsp;.&nbsp; | &nbsp;&nbsp;.&nbsp; | &nbsp;&nbsp;.&nbsp; | &nbsp;&nbsp;.&nbsp; | &nbsp;&nbsp;.&nbsp; | &nbsp;&nbsp;.&nbsp; | &nbsp;&nbsp;.&nbsp; | &nbsp;&nbsp;.&nbsp; | &nbsp;&nbsp;.&nbsp; |  &nbsp;&nbsp;2&nbsp; | &nbsp;&nbsp;DIYLB_top_A.stl |
| &nbsp;&nbsp;2&nbsp; | &nbsp;&nbsp;.&nbsp; | &nbsp;&nbsp;.&nbsp; | &nbsp;&nbsp;.&nbsp; | &nbsp;&nbsp;.&nbsp; | &nbsp;&nbsp;.&nbsp; | &nbsp;&nbsp;.&nbsp; | &nbsp;&nbsp;.&nbsp; | &nbsp;&nbsp;.&nbsp; | &nbsp;&nbsp;.&nbsp; | &nbsp;&nbsp;.&nbsp; | &nbsp;&nbsp;.&nbsp; | &nbsp;&nbsp;.&nbsp; | &nbsp;&nbsp;.&nbsp; | &nbsp;&nbsp;.&nbsp; | &nbsp;&nbsp;.&nbsp; | &nbsp;&nbsp;.&nbsp; | &nbsp;&nbsp;.&nbsp; | &nbsp;&nbsp;.&nbsp; | &nbsp;&nbsp;.&nbsp; | &nbsp;&nbsp;.&nbsp; | &nbsp;&nbsp;.&nbsp; |  &nbsp;&nbsp;2&nbsp; | &nbsp;&nbsp;DIYLB_top_B.stl |
| &nbsp;&nbsp;4&nbsp; | &nbsp;&nbsp;1&nbsp; | &nbsp;&nbsp;1&nbsp; | &nbsp;&nbsp;.&nbsp; | &nbsp;&nbsp;1&nbsp; | &nbsp;&nbsp;1&nbsp; | &nbsp;&nbsp;4&nbsp; | &nbsp;&nbsp;3&nbsp; | &nbsp;&nbsp;1&nbsp; | &nbsp;&nbsp;4&nbsp; | &nbsp;&nbsp;.&nbsp; | &nbsp;&nbsp;4&nbsp; | &nbsp;&nbsp;4&nbsp; | &nbsp;&nbsp;.&nbsp; | &nbsp;&nbsp;.&nbsp; | &nbsp;&nbsp;.&nbsp; | &nbsp;&nbsp;.&nbsp; | &nbsp;&nbsp;.&nbsp; | &nbsp;&nbsp;.&nbsp; | &nbsp;&nbsp;8&nbsp; | &nbsp;&nbsp;.&nbsp; | &nbsp;&nbsp;.&nbsp; | &nbsp;&nbsp;36&nbsp; | &nbsp;&nbsp;Total 3D printed parts count |

<span></span>
[Top](#TOP)

---

## 2 x DIYLB Top Assembly
### Vitamins
|Qty|Description|
|---:|:---|
|4| Screw M6 cap x 20mm|
|4| Washer  M6 x 12.5mm x 1.5mm|

### 3D Printed parts

| 2 x DIYLB_top_A.stl | 2 x DIYLB_top_B.stl |
|---|---|
| DIYLB_top_A.stl | DIYLB_top_B.stl 

### Assembly instructions
DIYLB_top_assembly

1. Cut a M6 thread into the top of the vertical 20x20 extrusions 
2. Attach the top holders
3. Secure the top holders with M6 screws

DIYLB_top_assembled

<span></span>
[Top](#TOP)

---

## DIYLB Carriage D Assembly
### Vitamins
|Qty|Description|
|---:|:---|
|1| Linear rail carriage MGN7C|
|2| Nut M3 x 2.4mm |
|4| Screw M2 cap x 10mm|
|2| Screw M3 pan x 12mm|
|1| Screw M4 cap x 12mm|
|1| Screw M6 pan x 20mm|
|1| T-Nut (20x20)|
|1| T8-Nut (narrow)|
|4| Washer  M2 x 5mm x 0.3mm|
|1| Washer  M4 x 9mm x 0.8mm|
|1| Washer  M6 x 12.5mm x 1.5mm|

### 3D Printed parts

| 1 x DIYLB_carriage_D.stl |
|---|
| DIYLB_carriage_D.stl 

### Assembly instructions
DIYLB_carriage_D_assembly

1. Attatch T8-nut to the carriage holder, using M3 screws,
2. Attatch the rail carriage to the carriage holder using M2 screws.
3. Put a T-nuts into the mounting hole.

DIYLB_carriage_D_assembled

<span></span>
[Top](#TOP)

---

## DIYLB Carriage C Assembly
### Vitamins
|Qty|Description|
|---:|:---|
|1| Linear rail carriage MGN7C|
|2| Nut M3 x 2.4mm |
|4| Screw M2 cap x 10mm|
|2| Screw M3 pan x 12mm|
|1| Screw M4 cap x 12mm|
|1| Screw M6 pan x 20mm|
|1| T-Nut (20x20)|
|1| T8-Nut (narrow)|
|4| Washer  M2 x 5mm x 0.3mm|
|1| Washer  M4 x 9mm x 0.8mm|
|1| Washer  M6 x 12.5mm x 1.5mm|

### 3D Printed parts

| 1 x DIYLB_carriage_C.stl |
|---|
| DIYLB_carriage_C.stl 

### Assembly instructions
DIYLB_carriage_C_assembly

1. Attatch T8-nut to the carriage holder, using M3 screws,
2. Attatch the rail carriage to the carriage holder using M2 screws.
3. Put a T-nuts into the mounting hole.

DIYLB_carriage_C_assembled

<span></span>
[Top](#TOP)

---

## 2 x DIYLB Carriage AB Assembly
### Vitamins
|Qty|Description|
|---:|:---|
|2| Extrusion E2020 x 235mm|

### Sub-assemblies

| 1 x DIYLB_carriage_A_assembly | 1 x DIYLB_carriage_B_assembly | 1 x DIYLB_carriage_C_assembly |
|---|---|---|
| DIYLB_carriage_A_assembled | DIYLB_carriage_B_assembled | DIYLB_carriage_C_assembled 

| 1 x DIYLB_carriage_D_assembly |
|---|
| DIYLB_carriage_D_assembled 

### Assembly instructions
DIYLB_carriage_AB_assembly

1. Cut a M6 thread into both ends of the extrusion,
2. Attatch attxh the carriage holders

DIYLB_carriage_AB_assembled

<span></span>
[Top](#TOP)

---

## DIYLB Carriage B Assembly
### Vitamins
|Qty|Description|
|---:|:---|
|1| Linear rail carriage MGN7C|
|2| Nut M3 x 2.4mm |
|4| Screw M2 cap x 10mm|
|2| Screw M3 pan x 12mm|
|1| Screw M4 cap x 12mm|
|1| Screw M6 pan x 20mm|
|1| T-Nut (20x20)|
|1| T8-Nut (narrow)|
|4| Washer  M2 x 5mm x 0.3mm|
|1| Washer  M4 x 9mm x 0.8mm|
|1| Washer  M6 x 12.5mm x 1.5mm|

### 3D Printed parts

| 1 x DIYLB_carriage_B.stl |
|---|
| DIYLB_carriage_B.stl 

### Assembly instructions
DIYLB_carriage_B_assembly

1. Attatch T8-nut to the carriage holder, using M3 screws,
2. Attatch the rail carriage to the carriage holder using M2 screws.
3. Put a T-nuts into the mounting hole.

DIYLB_carriage_B_assembled

<span></span>
[Top](#TOP)

---

## DIYLB Carriage A Assembly
### Vitamins
|Qty|Description|
|---:|:---|
|1| Linear rail carriage MGN7C|
|2| Nut M3 x 2.4mm |
|4| Screw M2 cap x 10mm|
|2| Screw M3 pan x 12mm|
|1| Screw M4 cap x 12mm|
|1| Screw M6 pan x 20mm|
|1| T-Nut (20x20)|
|1| T8-Nut (narrow)|
|4| Washer  M2 x 5mm x 0.3mm|
|1| Washer  M4 x 9mm x 0.8mm|
|1| Washer  M6 x 12.5mm x 1.5mm|

### 3D Printed parts

| 1 x DIYLB_carriage_A.stl |
|---|
| DIYLB_carriage_A.stl 

### Assembly instructions
DIYLB_carriage_A_assembly

1. Attatch T8-nut to the carriage holder, using M3 screws,
2. Attatch the rail carriage to the carriage holder using M2 screws.
3. Put a T-nuts into the mounting hole.

DIYLB_carriage_A_assembled

<span></span>
[Top](#TOP)

---

## 4 x DIYLB Rail Assembly
### Vitamins
|Qty|Description|
|---:|:---|
|4| Extrusion E2020 x 70mm|
|4| Linear rail MGN7 x 70mm|
|20| Nut M2 x 1.6mm |
|20| Screw M2 cap x  6mm|

### 3D Printed parts

| 4 x DIYLB_rail.stl |
|---|
| DIYLB_rail.stl 

### Assembly instructions
DIYLB_rail_assembly

1. Insert the M2 nuts into the printed holder.
2. Attach the rail loosely.
3. Slide the printed holder into the 20x20 extrusion and tighten the screws.

DIYLB_rail_assembled

<span></span>
[Top](#TOP)

---

## DIYLB Crank Assembly
### Vitamins
|Qty|Description|
|---:|:---|
|2| Ball bearing 608-2RS 8mm x 22mm x 7mm|
|1| Extrusion E2040 x 60mm|
|1| Extrusion E2040 x 70mm|
|2| L-Bracket (20x20)|
|1| Nut M8 x 6.5mm |
|2| Pulley GT2 idler smooth 12mm|
|1| Pulley GT2OB 20 teeth|
|6| Screw M3 grub x  6mm|
|2| Screw M4 cap x 15mm|
|4| Screw M4 dome x  8mm|
|3| Screw M8 hex x 50mm|
|4| T-Nut (20x20)|
|2| T-Nut (20x20)|
|6| Washer  M4 x 9mm x 0.8mm|

### 3D Printed parts

| 1 x DIYLB_crank.stl | 2 x DIYLB_crank_bearing.stl |
|---|---|
| DIYLB_crank.stl | DIYLB_crank_bearing.stl 

### Assembly instructions
DIYLB_crank_assembly

1. Connect the two 20x40 extrusions with L-brackets.
2. Assemble the axis as illustrated.
3. Slide the printed holders over the vertical 20x40 extrusion
   (and loosely insert the timing belt).
4. Move the two printed holders as far apart as possible and tighten the screws.
5. Slide two idlers on T-nuts onto the top slot of the horizontal 20x40 extrusion.

DIYLB_crank_assembled

<span></span>
[Top](#TOP)

---

## DIYLB Idler Assembly
### Vitamins
|Qty|Description|
|---:|:---|
|1| Nut M5 x 4mm |
|1| Pulley GT2 idler 20 teeth|
|2| Screw M4 cap x 12mm|
|1| Screw M5 cap x 28mm|
|2| T-Nut (20x20)|
|2| Washer  M4 x 9mm x 0.8mm|
|1| Washer  M5 x 10mm x 1mm|

### 3D Printed parts

| 1 x DIYLB_idler.stl |
|---|
| DIYLB_idler.stl 

### Assembly instructions
DIYLB_idler_assembly

1. Screw the idler onto the holder.
2. Attach two T-nuts with screws and washers.

DIYLB_idler_assembled

<span></span>
[Top](#TOP)

---

## 4 x DIYLB Lower Bearing Assembly
### Vitamins
|Qty|Description|
|---:|:---|
|4| Ball bearing 608-2RS 8mm x 22mm x 7mm|
|4| Euro-Cent coin|
|4| Pulley GT2OB 20 teeth|
|8| Screw M3 grub x  6mm|
|8| Screw M4 cap x 12mm|
|8| T-Nut (20x20)|
|4| Threaded rod M8 x 100mm|
|8| Washer  M4 x 9mm x 0.8mm|

### 3D Printed parts

| 4 x DIYLB_lower_bearing.stl |
|---|
| DIYLB_lower_bearing.stl 

### Assembly instructions
DIYLB_lower_bearing_assembly

1. Put a EuroCent coin in the bottom of the lower ball bearing holder.
2. Squeze the ball bearing into the holder.
3. Attach two T-nuts with screws and washers.
4. Put the pulley loosely onto the threaded rod and insert them into the ball bearingpulles.  

DIYLB_lower_bearing_assembled

<span></span>
[Top](#TOP)

---

## DIYLB Base Right Assembly
### Vitamins
|Qty|Description|
|---:|:---|
|1| Extrusion E2020 x 300mm|
|2| L-Bracket (20x20)|
|4| Screw M3 grub x  6mm|

### Sub-assemblies

| 1 x DIYLB_idler_assembly | 2 x DIYLB_lower_bearing_assembly |
|---|---|
| DIYLB_idler_assembled | DIYLB_lower_bearing_assembled 

### Assembly instructions
DIYLB_base_right_assembly

1. Slide two L-brackets onto the top slot of the 20x20 extrusion.
2. Slide the two holders for the ball bearings onto the lef-thand slot
   of the 20x20 extrusion.
3. Attach the idler mount

DIYLB_base_right_assembled

<span></span>
[Top](#TOP)

---

## 4 x DIYLB Magnet Cover Assembly
### Vitamins
|Qty|Description|
|---:|:---|
|4| Euro-Cent coin|

### 3D Printed parts

| 4 x DIYLB_magnet_cover.stl |
|---|
| DIYLB_magnet_cover.stl 

### Assembly instructions
DIYLB_magnet_cover_assembly

1. insert cent coin during print.

DIYLB_magnet_cover_assembled

<span></span>
[Top](#TOP)

---

## 4 x DIYLB Magnet Assembly
### Vitamins
|Qty|Description|
|---:|:---|
|4| Neodym Magnet (D=20,H=4.5)|
|8| Screw M4 cap x 12mm|
|8| T-Nut (20x20)|
|8| Washer  M4 x 9mm x 0.8mm|

### 3D Printed parts

| 4 x DIYLB_magnet.stl |
|---|
| DIYLB_magnet.stl 

### Sub-assemblies

| 4 x DIYLB_magnet_cover_assembly |
|---|
| DIYLB_magnet_cover_assembled 

### Assembly instructions
DIYLB_magnet_assembly

1. Squeze the magnet into the holder.
2. Attach two T-nuts with screws and washers.
3. Put the covers on top of the magnets.

DIYLB_magnet_assembled

<span></span>
[Top](#TOP)

---

## 2 x DIYLB Base Center Assembly
### Vitamins
|Qty|Description|
|---:|:---|
|2| Extrusion E2020 x 320mm|

### Sub-assemblies

| 4 x DIYLB_magnet_assembly |
|---|
| DIYLB_magnet_assembled 

### Assembly instructions
DIYLB_base_center_assembly

1. Attach two magnet holders to the 320mm 20x20 extrusion.

DIYLB_base_center_assembled

<span></span>
[Top](#TOP)

---

## DIYLB Base Left Assembly
### Vitamins
|Qty|Description|
|---:|:---|
|1| Extrusion E2020 x 300mm|
|4| L-Bracket (20x20)|
|8| Screw M3 grub x  6mm|

### Sub-assemblies

| 2 x DIYLB_lower_bearing_assembly |
|---|
| DIYLB_lower_bearing_assembled 

### Assembly instructions
DIYLB_base_left_assembly

1. Slide two L-brackets onto the top slot of the 20x20 extrusion.
2. Slide the two holders for the ball bearings onto the right-hand slot
   of the 20x20 extrusion.
3. Slide two L-brackets onto the left-hand slot of the 20x20 extrusion.

DIYLB_base_left_assembled

<span></span>
[Top](#TOP)

---

## DIYLB Base Assembly
### Sub-assemblies

| 2 x DIYLB_base_center_assembly | 1 x DIYLB_base_left_assembly | 1 x DIYLB_base_right_assembly |
|---|---|---|
| DIYLB_base_center_assembled | DIYLB_base_left_assembled | DIYLB_base_right_assembled 

### Assembly instructions
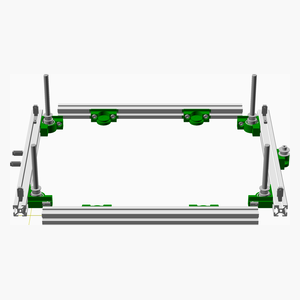
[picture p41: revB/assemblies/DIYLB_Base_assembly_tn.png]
DIYLB_Base_assembly


1. Attach all parts of the base frame
2. Tighten the screws of the bearing holders, connecting 20x20 extrusions

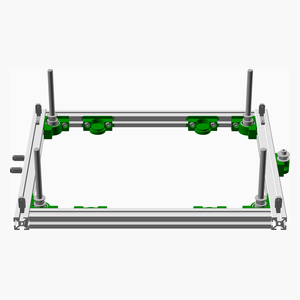
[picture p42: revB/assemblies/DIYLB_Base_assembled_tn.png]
DIYLB_Base_assembled


<span></span>
[Top](#TOP)

---

## DIYLB Crank To Base Assembly
### Sub-assemblies

| 1 x DIYLB_Base_assembly | 1 x DIYLB_crank_assembly |
|---|---|
| DIYLB_Base_assembled | DIYLB_crank_assembled 

### Assembly instructions
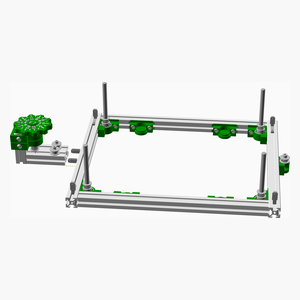
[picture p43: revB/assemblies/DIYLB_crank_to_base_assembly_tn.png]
DIYLB_crank_to_base_assembly


1. Attach the crank holder to the base of the frame  
2. Tighten the screws of the L-brackets

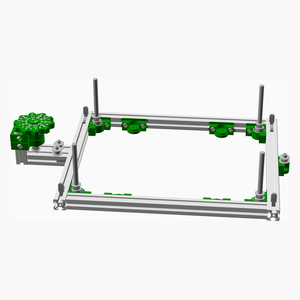
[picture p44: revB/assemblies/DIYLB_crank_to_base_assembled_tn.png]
DIYLB_crank_to_base_assembled


<span></span>
[Top](#TOP)

---

## DIYLB Columns To Base Assembly
### Sub-assemblies

| 1 x DIYLB_crank_to_base_assembly | 4 x DIYLB_rail_assembly |
|---|---|
| DIYLB_crank_to_base_assembled | DIYLB_rail_assembled 

### Assembly instructions
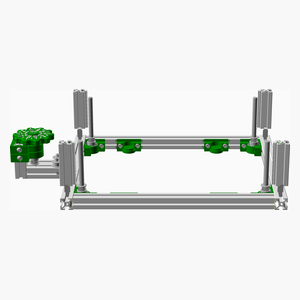
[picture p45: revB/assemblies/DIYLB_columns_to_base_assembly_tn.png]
DIYLB_columns_to_base_assembly


1. Attach the for columns to the base of the frame  
2. Tighten the screws of the L-brackets

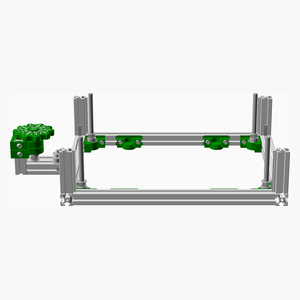
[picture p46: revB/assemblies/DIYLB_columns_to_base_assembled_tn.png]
DIYLB_columns_to_base_assembled


<span></span>
[Top](#TOP)

---

## DIYLB Bed To Columns Assembly
### Sub-assemblies

| 2 x DIYLB_carriage_AB_assembly | 1 x DIYLB_columns_to_base_assembly |
|---|---|
| DIYLB_carriage_AB_assembled | DIYLB_columns_to_base_assembled 

### Assembly instructions
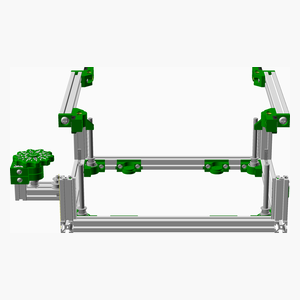
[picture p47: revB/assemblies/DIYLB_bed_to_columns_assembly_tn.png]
DIYLB_bed_to_columns_assembly


1. Thread the assembled carriage holders into the rails and rods of the Z-axis.

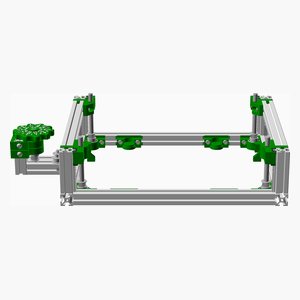
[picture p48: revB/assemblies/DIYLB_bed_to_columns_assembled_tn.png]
DIYLB_bed_to_columns_assembled


<span></span>
[Top](#TOP)

---

## DIYLB Beams To Bed Assembly
### Vitamins
|Qty|Description|
|---:|:---|
|1| Flat section 15mmx2mm, 272mm|
|4| Flat section 15mmx2mm, 316mm|

### 3D Printed parts

| 8 x DIYLB_beam_holder.stl |
|---|
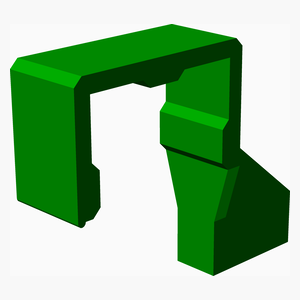
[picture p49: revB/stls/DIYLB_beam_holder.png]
DIYLB_beam_holder.stl
|  

### Sub-assemblies

| 1 x DIYLB_bed_to_columns_assembly |
|---|
| DIYLB_bed_to_columns_assembled 

### Assembly instructions
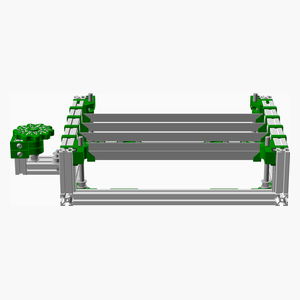
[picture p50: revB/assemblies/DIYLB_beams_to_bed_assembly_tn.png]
DIYLB_beams_to_bed_assembly


1. Attach the beam holders to the horizontal 20x20 extrusions of the bed.
2. Slide the beams into the beam holders

DIYLB_beams_to_bed_assembled

<span></span>
[Top](#TOP)

---

## DIYLB Top To Columns Assembly
### Sub-assemblies

| 1 x DIYLB_beams_to_bed_assembly | 2 x DIYLB_top_assembly |
|---|---|
| DIYLB_beams_to_bed_assembled | DIYLB_top_assembled 

### Assembly instructions
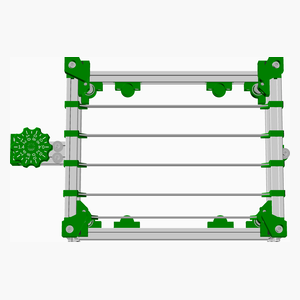
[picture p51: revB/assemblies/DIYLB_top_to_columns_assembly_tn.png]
DIYLB_top_to_columns_assembly


1. Attach the top extrusions to the rest of the frame.

DIYLB_top_to_columns_assembled

<span></span>
[Top](#TOP)

---

## DIYLB Belt Assembly
### Vitamins
|Qty|Description|
|---:|:---|
|1| Belt GT2 x 6mm x 1222mm|

### Sub-assemblies

| 1 x DIYLB_top_to_columns_assembly |
|---|
| DIYLB_top_to_columns_assembled 

### Assembly instructions
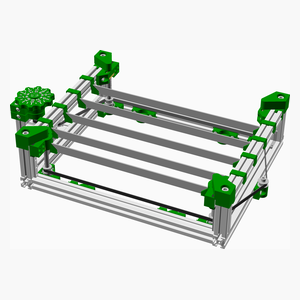
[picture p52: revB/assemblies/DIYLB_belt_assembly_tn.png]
DIYLB_belt_assembly


1. Insert the timing belt
2. Level the bed by turning the thraded rods, before tightening the pulleys 

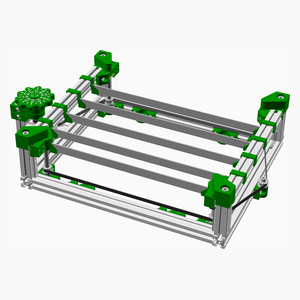
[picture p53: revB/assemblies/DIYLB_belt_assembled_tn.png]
DIYLB_belt_assembled


<span></span>
[Top](#TOP)

---
Finished!

<span></span>
[Top](#TOP)

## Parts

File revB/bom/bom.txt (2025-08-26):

Vitamins:
                                     D                              
                D                    i                          D   
                i                    y     D     D              i   
             D  y                    l     i     i     D        y   
    D        i  l     D              b     y     y     i        l   
    i     D  y  b     i  D  D  D  D        l     l     y        b   
    y  D  i  l        y  i  i  i  i  c     b     b     l            
    l  i  y  b  b     l  y  y  y  y  o                 b        t   
    b  y  l     e     b  l  l  l  l  l     c     l              o   
       l  b  b  d        b  b  b  b  u     r     o  D  m        p   
    b  b     e        c              m  D  a  D  w  i  a            
 D  a     b  a  t  D  a  c  c  c  c  n  i  n  i  e  y  g  D     t   
 i  s  b  a  m  o  i  r  a  a  a  a  s  y  k  y  r  l  n  i  D  o   
 y  e  a  s  s     y  r  r  r  r  r     l     l     b  e  y  i      
 l     s  e     c  l  i  r  r  r  r  t  b  t  b  b     t  l  y  c   
 b  c  e     t  o  b  a  i  i  i  i  o     o     e  m     b  l  o   
    e     r  o  l     g  a  a  a  a     c     i  a  a  c     b  l   
 b  n  l  i     u  b  e  g  g  g  g  b  r  b  d  r  g  o  r     u  M
 a  t  e  g  b  m  e     e  e  e  e  a  a  a  l  i  n  v  a  t  m  a
 s  e  f  h  e  n  l  a              s  n  s  e  n  e  e  i  o  n  i
 e  r  t  t  d  s  t  b  a  b  c  d  e  k  e  r  g  t  r  l  p  s  n
  |  |  |  |  |  |  |  |  |  |  |  |  | 2|  |  | 4|  |  |  |  |  |  |  6 Ball bearing 608-2RS 8mm x 22mm x 7mm
  |  |  |  |  |  | 1|  |  |  |  |  |  |  |  |  |  |  |  |  |  |  |  |  1 Belt GT2 x 6mm x 1222mm
  |  |  |  |  |  |  |  | 1| 1| 1| 1|  |  |  |  |  |  |  |  |  |  |  |  4 Linear rail carriage MGN7C
  |  |  |  |  |  |  |  |  |  |  |  |  |  |  |  | 4|  | 4|  |  |  |  |  8 Euro-Cent coin
  |  |  |  |  |  |  | 2|  |  |  |  |  |  |  |  |  |  |  |  |  |  |  |  2 Extrusion E2020 x 235mm
  |  | 1| 1|  |  |  |  |  |  |  |  |  |  |  |  |  |  |  |  |  |  |  |  2 Extrusion E2020 x 300mm
  | 2|  |  |  |  |  |  |  |  |  |  |  |  |  |  |  |  |  |  |  |  |  |  2 Extrusion E2020 x 320mm
  |  |  |  |  |  |  |  |  |  |  |  |  |  |  |  |  |  |  | 4|  |  |  |  4 Extrusion E2020 x 70mm
  |  |  |  |  |  |  |  |  |  |  |  |  | 1|  |  |  |  |  |  |  |  |  |  1 Extrusion E2040 x 60mm
  |  |  |  |  |  |  |  |  |  |  |  |  | 1|  |  |  |  |  |  |  |  |  |  1 Extrusion E2040 x 70mm
  |  |  |  | 1|  |  |  |  |  |  |  |  |  |  |  |  |  |  |  |  |  |  |  1 Flat section 15mmx2mm, 272mm
  |  |  |  | 4|  |  |  |  |  |  |  |  |  |  |  |  |  |  |  |  |  |  |  4 Flat section 15mmx2mm, 316mm
  |  | 4| 2|  |  |  |  |  |  |  |  |  | 2|  |  |  |  |  |  |  |  |  |  8 L-Bracket (20x20)
  |  |  |  |  |  |  |  |  |  |  |  |  |  |  |  |  | 4|  |  |  |  |  |  4 Neodym Magnet (D=20,H=4.5)
  |  |  |  |  |  |  |  |  |  |  |  |  |  |  |  |  |  |  |20|  |  |  | 20 Nut M2 x 1.6mm 
  |  |  |  |  |  |  |  | 2| 2| 2| 2|  |  |  |  |  |  |  |  |  |  |  |  8 Nut M3 x 2.4mm 
  |  |  |  |  |  |  |  |  |  |  |  |  |  |  | 1|  |  |  |  |  |  |  |  1 Nut M5 x 4mm 
  |  |  |  |  |  |  |  |  |  |  |  |  | 1|  |  |  |  |  |  |  |  |  |  1 Nut M8 x 6.5mm 
  |  |  |  |  |  |  |  |  |  |  |  |  | 2|  |  |  |  |  |  |  |  |  |  2 Pulley GT2 idler smooth 12mm
  |  |  |  |  |  |  |  |  |  |  |  |  | 1|  |  | 4|  |  |  |  |  |  |  5 Pulley GT2OB 20 teeth
  |  |  |  |  |  |  |  |  |  |  |  |  |  |  | 1|  |  |  |  |  |  |  |  1 Pulley GT2 idler 20 teeth
  |  |  |  |  |  |  |  |  |  |  |  |  |  |  |  |  |  |  | 4|  |  |  |  4 Linear rail MGN7 x 70mm
  |  |  |  |  |  |  |  | 4| 4| 4| 4|  |  |  |  |  |  |  |  |  |  |  | 16 Screw M2 cap x 10mm
  |  |  |  |  |  |  |  |  |  |  |  |  |  |  |  |  |  |  |20|  |  |  | 20 Screw M2 cap x  6mm
  |  | 8| 4|  |  |  |  |  |  |  |  |  | 6|  |  | 8|  |  |  |  |  |  | 26 Screw M3 grub x  6mm
  |  |  |  |  |  |  |  | 2| 2| 2| 2|  |  |  |  |  |  |  |  |  |  |  |  8 Screw M3 pan x 12mm
  |  |  |  |  |  |  |  | 1| 1| 1| 1|  |  |  | 2| 8| 8|  |  |  |  |  | 22 Screw M4 cap x 12mm
  |  |  |  |  |  |  |  |  |  |  |  |  | 2|  |  |  |  |  |  |  |  |  |  2 Screw M4 cap x 15mm
  |  |  |  |  |  |  |  |  |  |  |  |  | 4|  |  |  |  |  |  |  |  |  |  4 Screw M4 dome x  8mm
  |  |  |  |  |  |  |  |  |  |  |  |  |  |  | 1|  |  |  |  |  |  |  |  1 Screw M5 cap x 28mm
  |  |  |  |  |  |  |  |  |  |  |  |  |  |  |  |  |  |  |  | 4|  |  |  4 Screw M6 cap x 20mm
  |  |  |  |  |  |  |  | 1| 1| 1| 1|  |  |  |  |  |  |  |  |  |  |  |  4 Screw M6 pan x 20mm
  |  |  |  |  |  |  |  |  |  |  |  |  | 3|  |  |  |  |  |  |  |  |  |  3 Screw M8 hex x 50mm
  |  |  |  |  |  |  |  |  |  |  |  |  |  |  |  | 4|  |  |  |  |  |  |  4 Threaded rod M8 x 100mm
  |  |  |  |  |  |  |  | 1| 1| 1| 1|  |  |  |  |  |  |  |  |  |  |  |  4 T8-Nut (narrow)
  |  |  |  |  |  |  |  | 1| 1| 1| 1|  |  |  | 2| 8| 8|  |  |  |  |  | 22 T-Nut (20x20)
  |  |  |  |  |  |  |  |  |  |  |  |  | 2|  |  |  |  |  |  |  |  |  |  2 T-Nut (20x20)
  |  |  |  |  |  |  |  |  |  |  |  |  | 4|  |  |  |  |  |  |  |  |  |  4 T-Nut (20x20)
  |  |  |  |  |  |  |  | 4| 4| 4| 4|  |  |  |  |  |  |  |  |  |  |  | 16 Washer  M2 x 5mm x 0.3mm
  |  |  |  |  |  |  |  | 1| 1| 1| 1|  | 6|  | 2| 8| 8|  |  |  |  |  | 28 Washer  M4 x 9mm x 0.8mm
  |  |  |  |  |  |  |  |  |  |  |  |  |  |  | 1|  |  |  |  |  |  |  |  1 Washer  M5 x 10mm x 1mm
  |  |  |  |  |  |  |  | 1| 1| 1| 1|  |  |  |  |  |  |  |  | 4|  |  |  8 Washer  M6 x 12.5mm x 1.5mm

Printed:
  |  |  |  | 8|  |  |  |  |  |  |  |  |  |  |  |  |  |  |  |  |  |  |  8 DIYLB_beam_holder.stl
  |  |  |  |  |  |  |  | 1|  |  |  |  |  |  |  |  |  |  |  |  |  |  |  1 DIYLB_carriage_A.stl
  |  |  |  |  |  |  |  |  | 1|  |  |  |  |  |  |  |  |  |  |  |  |  |  1 DIYLB_carriage_B.stl
  |  |  |  |  |  |  |  |  |  | 1|  |  |  |  |  |  |  |  |  |  |  |  |  1 DIYLB_carriage_C.stl
  |  |  |  |  |  |  |  |  |  |  | 1|  |  |  |  |  |  |  |  |  |  |  |  1 DIYLB_carriage_D.stl
  |  |  |  |  |  |  |  |  |  |  |  |  | 1|  |  |  |  |  |  |  |  |  |  1 DIYLB_crank.stl
  |  |  |  |  |  |  |  |  |  |  |  |  | 2|  |  |  |  |  |  |  |  |  |  2 DIYLB_crank_bearing.stl
  |  |  |  |  |  |  |  |  |  |  |  |  |  |  | 1|  |  |  |  |  |  |  |  1 DIYLB_idler.stl
  |  |  |  |  |  |  |  |  |  |  |  |  |  |  |  | 4|  |  |  |  |  |  |  4 DIYLB_lower_bearing.stl
  |  |  |  |  |  |  |  |  |  |  |  |  |  |  |  |  | 4|  |  |  |  |  |  4 DIYLB_magnet.stl
  |  |  |  |  |  |  |  |  |  |  |  |  |  |  |  |  |  | 4|  |  |  |  |  4 DIYLB_magnet_cover.stl
  |  |  |  |  |  |  |  |  |  |  |  |  |  |  |  |  |  |  | 4|  |  |  |  4 DIYLB_rail.stl
  |  |  |  |  |  |  |  |  |  |  |  |  |  |  |  |  |  |  |  | 2|  |  |  2 DIYLB_top_A.stl
  |  |  |  |  |  |  |  |  |  |  |  |  |  |  |  |  |  |  |  | 2|  |  |  2 DIYLB_top_B.stl

Assemblies:
  1 DIYLB_Base_assembly
  2 DIYLB_base_center_assemblies
  1 DIYLB_base_left_assembly
  1 DIYLB_base_right_assembly
  1 DIYLB_beams_to_bed_assembly
  1 DIYLB_bed_to_columns_assembly
  1 DIYLB_belt_assembly
  2 DIYLB_carriage_AB_assemblies
  1 DIYLB_carriage_A_assembly
  1 DIYLB_carriage_B_assembly
  1 DIYLB_carriage_C_assembly
  1 DIYLB_carriage_D_assembly
  1 DIYLB_columns_to_base_assembly
  1 DIYLB_crank_assembly
  1 DIYLB_crank_to_base_assembly
  1 DIYLB_idler_assembly
  4 DIYLB_lower_bearing_assemblies
  4 DIYLB_magnet_assemblies
  4 DIYLB_magnet_cover_assemblies
  4 DIYLB_rail_assemblies
  2 DIYLB_top_assemblies
  1 DIYLB_top_to_columns_assembly
  1 main_assembly

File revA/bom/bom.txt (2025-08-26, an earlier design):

Vitamins:
                            D                        
                D        D  i                 D      
                i     D  i  y     D  D        i  D   
                y     i  y  l     i  i        y  i   
    D           l     y  l  b     y  y        l  y   
    i     D     b     l  b        l  l        b  l   
    y  D  i           b     c     b  b           b   
    l  i  y     b        c  o                 t      
    b  y  l     e     c  a  l     c  l        o  u   
       l  b     d     a  r  u     r  o        p  p   
    b  b              r  r  m  D  a  w           p   
 D  a     b     t  D  r  i  n  i  n  e  D     t  e   
 i  s  b  a  D  o  i  i  a  s  y  k  r  i  D  o  r   
 y  e  a  s  i     y  a  g     l        y  i         
 l     s  e  y  c  l  g  e  t  b  t  b  l  y  c  b   
 b  c  e     l  o  b  e     o     o  e  b  l  o  e   
    e     r  b  l        r     c     a     b  l  a   
 b  n  l  i     u  b  l  i  b  r  b  r  r     u  r  M
 a  t  e  g  b  m  e  e  g  a  a  a  i  a  t  m  i  a
 s  e  f  h  e  n  l  f  h  s  n  s  n  i  o  n  n  i
 e  r  t  t  d  s  t  t  t  e  k  e  g  l  p  s  g  n
  |  |  |  |  |  |  |  |  |  | 2|  | 4|  |  |  | 4|  | 10 Ball bearing 608-2RS 8mm x 22mm x 7mm
  |  |  |  |  |  | 1|  |  |  |  |  |  |  |  |  |  |  |  1 Belt GT2 x 6mm x 1104mm
  |  |  |  |  |  |  | 2| 2|  |  |  |  |  |  |  |  |  |  4 Linear rail carriage MGN7C
  |  |  |  |  |  |  |  |  |  |  |  | 4|  |  |  |  |  |  4 Euro-Cent coin
  |  |  |  | 4|  |  |  |  |  |  |  |  |  |  |  |  |  |  4 Extrusion E2020 x 260mm
  |  | 1| 1|  |  |  |  |  |  |  |  |  |  | 2|  |  |  |  4 Extrusion E2020 x 300mm
  | 2|  |  | 2|  |  |  |  |  |  |  |  |  |  |  |  |  |  4 Extrusion E2020 x 320mm
  |  |  |  |  |  |  |  |  |  |  |  |  | 4|  |  |  |  |  4 Extrusion E2020 x 70mm
  |  |  |  |  |  |  |  |  |  | 1|  |  |  |  |  |  |  |  1 Extrusion E2040 x 60mm
  |  |  |  |  |  |  |  |  |  | 1|  |  |  |  |  |  |  |  1 Extrusion E2040 x 70mm
  |  | 8| 6|12|  |  |  |  |  | 2|  |  |  |  |  |  |  | 28 L-Bracket (20x20)
  |  |  |  |  |  |  |  |  |  |  |  |  |20|  |  |  |  | 20 Nut M2 x 1.6mm 
  |  |  |  |  |  |  | 4| 4|  |  |  |  |  |  |  |  |  |  8 Nut M3 x 2.4mm 
  |  |  |  |  |  |  |  |  |  | 1|  |  |  |  |  |  |  |  1 Nut M8 x 6.5mm 
  |  | 2|  |  |  |  |  |  |  |  |  |  |  |  |  |  |  |  2 Pulley GT2 idler smooth 12mm
  |  |  |  |  |  |  |  |  |  | 1|  | 4|  |  |  |  |  |  5 Pulley GT2OB 20 teeth
  |  |  |  |  |  |  |  |  |  |  |  |  | 4|  |  |  |  |  4 Linear rail MGN7 x 70mm
  |  |  |  |  |  |  | 8| 8|  |  |  |  |  |  |  |  |  | 16 Screw M2 cap x 10mm
  |  |  |  |  |  |  |  |  |  |  |  |  |20|  |  |  |  | 20 Screw M2 cap x  6mm
  |  |  |  |  |  |  |  |  |  |  |  |  |  |  |  | 4|  |  4 Screw M3 grub x  4mm
  |  |16|12|24|  |  |  |  |  | 6|  | 8|  |  |  |  |  | 66 Screw M3 grub x  6mm
  |  |  |  |  |  |  | 4| 4|  |  |  |  |  |  |  |  |  |  8 Screw M3 pan x 16mm
  |  |  |  |  |  |  | 6| 6|  |  |  | 8|  |  |  | 8|  | 28 Screw M4 cap x 12mm
  |  | 2|  |  |  |  |  |  |  |  |  |  |  |  |  |  |  |  2 Screw M4 cap x 20mm
  | 4|  |  |  |  |  |  |  |  | 4|  |  |  |  |  |  |  |  8 Screw M4 dome x  8mm
  |  |  |  |  |  |  |  |  |  | 3|  |  |  |  |  |  |  |  3 Screw M8 hex x 50mm
  |  |  |  |  |  |  |  |  |  |  |  | 4|  |  |  |  |  |  4 Threaded rod M8 x 100mm
  |  |  |  |  |  |  |  |  |  |  |  |  |  |  |  | 4|  |  4 Lock ring (8mm)
  |  |  |  |  |  |  | 2| 2|  |  |  |  |  |  |  |  |  |  4 T8-Nut (narrow)
  |  |  |  |  |  |  | 6| 6|  |  |  | 8|  |  |  | 8|  | 28 T-Nut (20x20)
  |  | 2|  |  |  |  |  |  |  |  |  |  |  |  |  |  |  |  2 T-Nut (20x20)
  | 4|  |  |  |  |  |  |  |  | 4|  |  |  |  |  |  |  |  8 T-Nut (20x20)
  |  |  |  |  |  |  | 8| 8|  |  |  |  |  |  |  |  |  | 16 Washer  M2 x 5mm x 0.3mm
  | 4| 2|  |  |  |  | 6| 6|  | 4|  | 8|  |  |  | 8|  | 38 Washer  M4 x 9mm x 0.8mm

Printed:
  |  |  |  |  |  |  | 2|  |  |  |  |  |  |  |  |  |  |  2 DIYLB_carriage_left.stl
  |  |  |  |  |  |  |  | 2|  |  |  |  |  |  |  |  |  |  2 DIYLB_carriage_right.stl
  |  |  |  |  |  |  |  |  |  | 1|  |  |  |  |  |  |  |  1 DIYLB_crank.stl
  |  |  |  |  |  |  |  |  |  | 2|  |  |  |  |  |  |  |  2 DIYLB_crank_bearing.stl
  |  |  |  |  |  |  |  |  |  |  |  | 4|  |  |  |  |  |  4 DIYLB_lower_bearing.stl
  |  |  |  |  |  |  |  |  |  |  |  |  | 4|  |  |  |  |  4 DIYLB_rail.stl
  |  |  |  |  |  |  |  |  |  |  |  |  |  |  |  | 4|  |  4 DIYLB_upper_bearing.stl

Assemblies:
  1 DIYLB_Base_assembly
  1 DIYLB_base_center_assembly
  1 DIYLB_base_left_assembly
  1 DIYLB_base_right_assembly
  1 DIYLB_bed_assembly
  1 DIYLB_bed_to_columns_assembly
  1 DIYLB_belt_assembly
  2 DIYLB_carriage_left_assemblies
  2 DIYLB_carriage_right_assemblies
  1 DIYLB_columns_to_base_assembly
  1 DIYLB_crank_assembly
  1 DIYLB_crank_to_base_assembly
  4 DIYLB_lower_bearing_assemblies
  4 DIYLB_rail_assemblies
  1 DIYLB_top_assembly
  1 DIYLB_top_to_columns_assembly
  4 DIYLB_upper_bearing_assemblies
  1 main_assembly

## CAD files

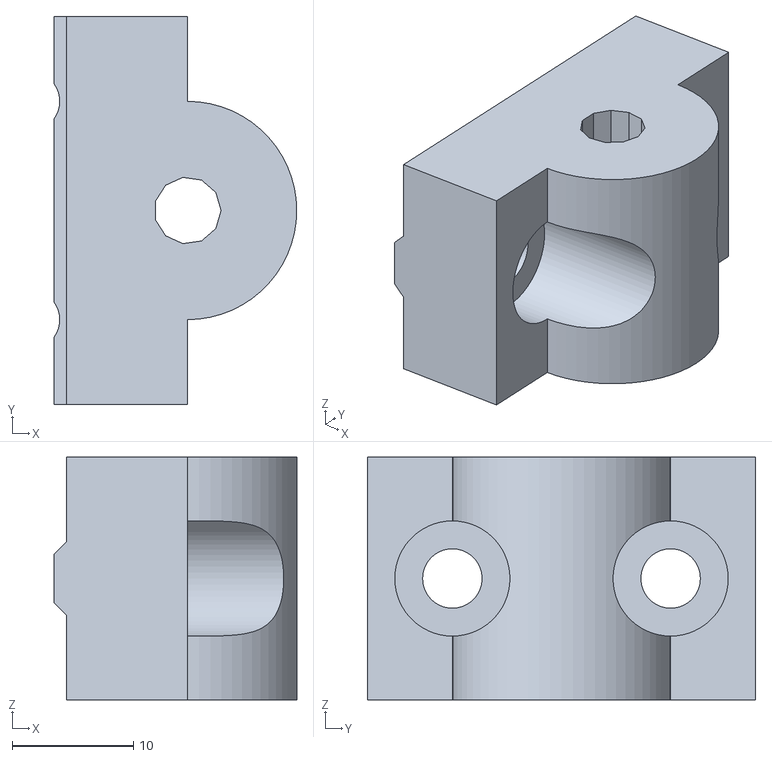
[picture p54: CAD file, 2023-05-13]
revB/stls/DIYLB_idler.stl
20.0 x 32.0 x 20.0

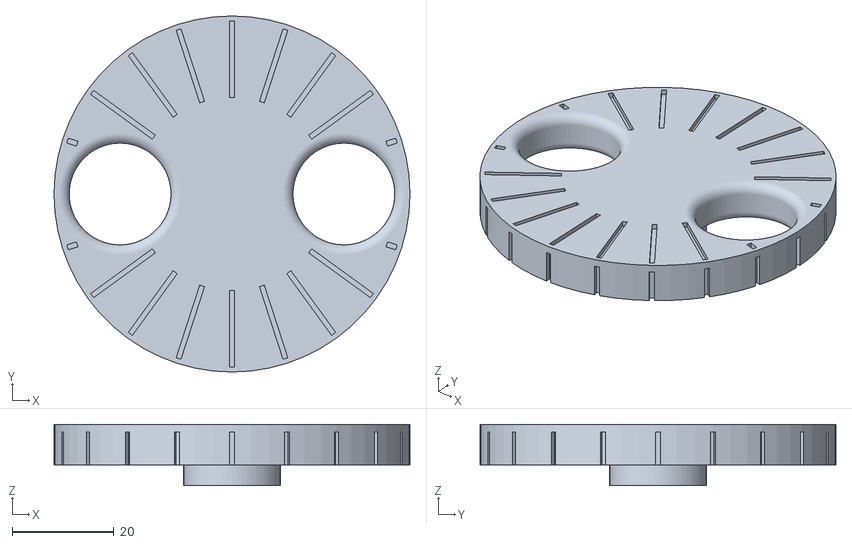
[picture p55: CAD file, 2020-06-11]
stls/DIYLB_crank.stl
70.0 x 70.0 x 12.0

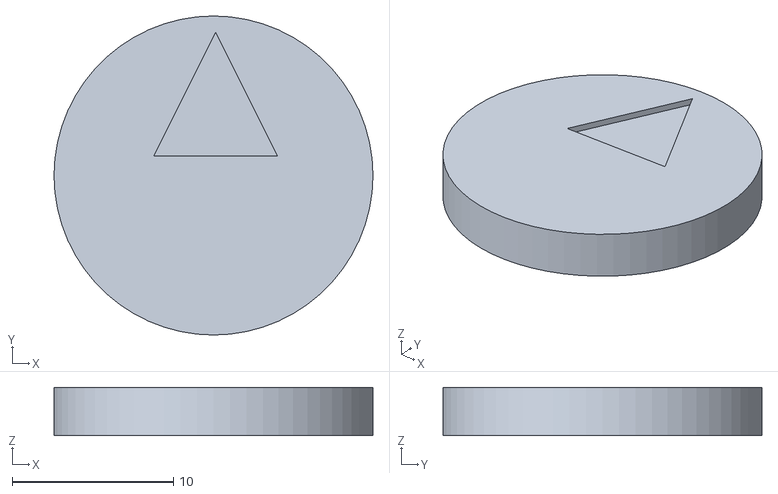
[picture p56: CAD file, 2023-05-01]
revB/stls/DIYLB_magnet_cover.stl
19.8 x 19.8 x 3.00

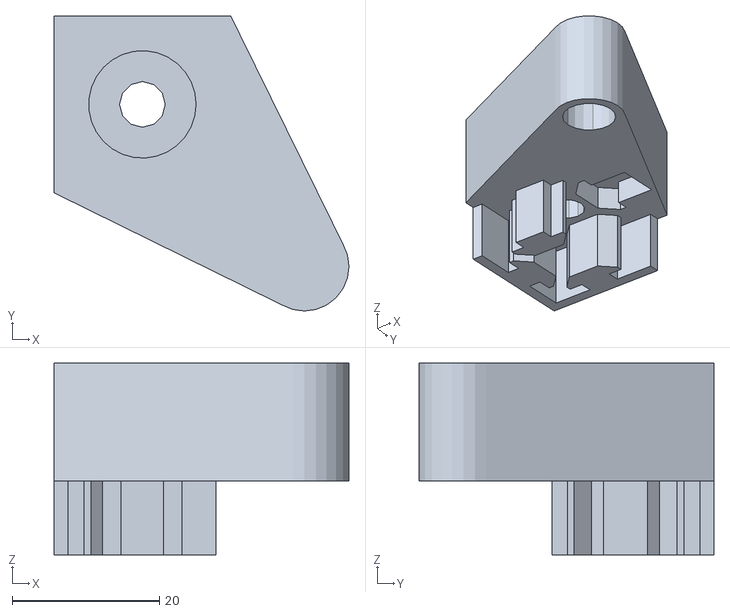
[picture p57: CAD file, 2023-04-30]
revB/stls/DIYLB_top_B.stl
40.1 x 40.1 x 26.0

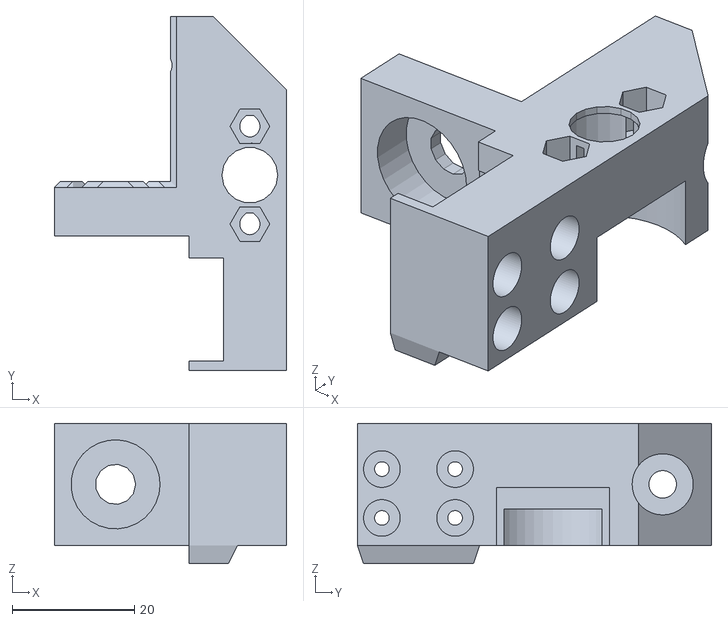
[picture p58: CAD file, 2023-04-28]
revB/stls/DIYLB_carriage_C.stl
38.0 x 58.0 x 23.0

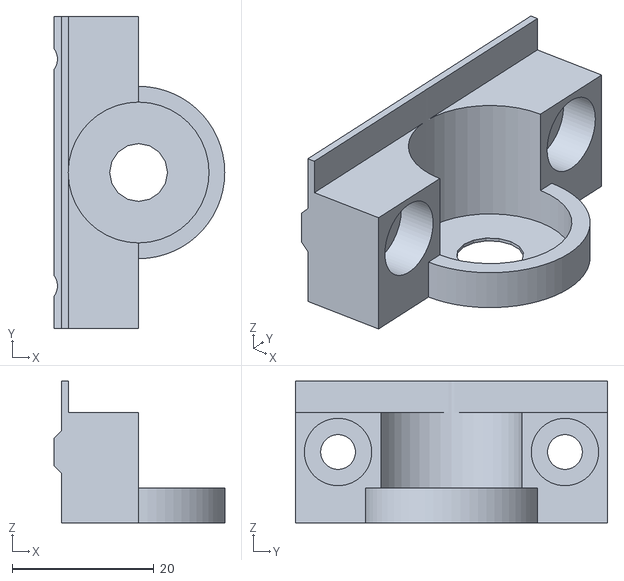
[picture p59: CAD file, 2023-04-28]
revB/stls/DIYLB_magnet.stl
24.1 x 44.0 x 20.0

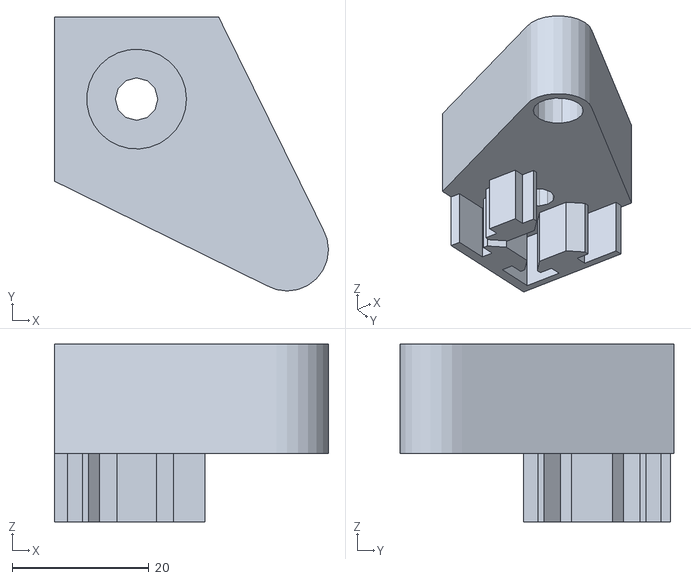
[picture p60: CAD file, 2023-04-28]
revB/stls/DIYLB_top_back.stl
40.1 x 40.1 x 26.0

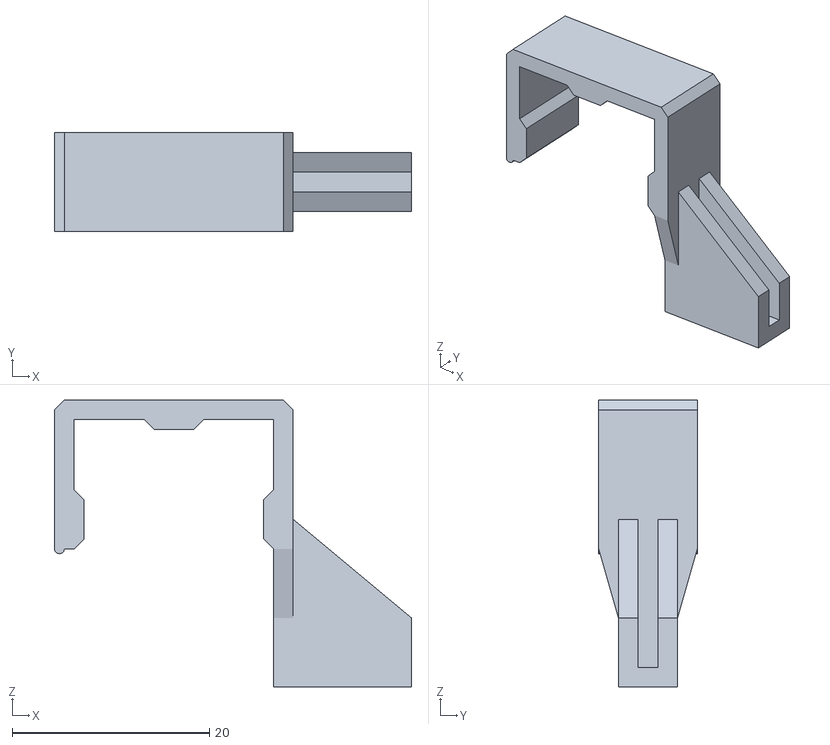
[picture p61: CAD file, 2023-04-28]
revB/stls/DIYLB_beam_holder.stl
36.2 x 10.0 x 29.1

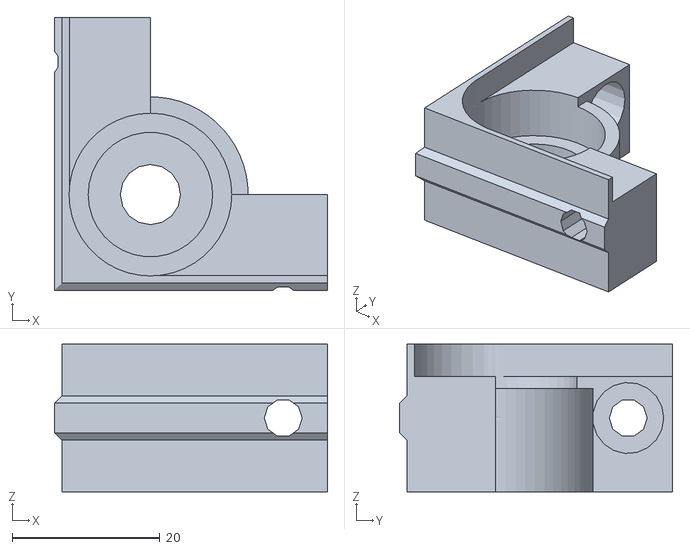
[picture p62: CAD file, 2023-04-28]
revB/stls/DIYLB_lower_bearing.stl
37.0 x 37.0 x 20.0

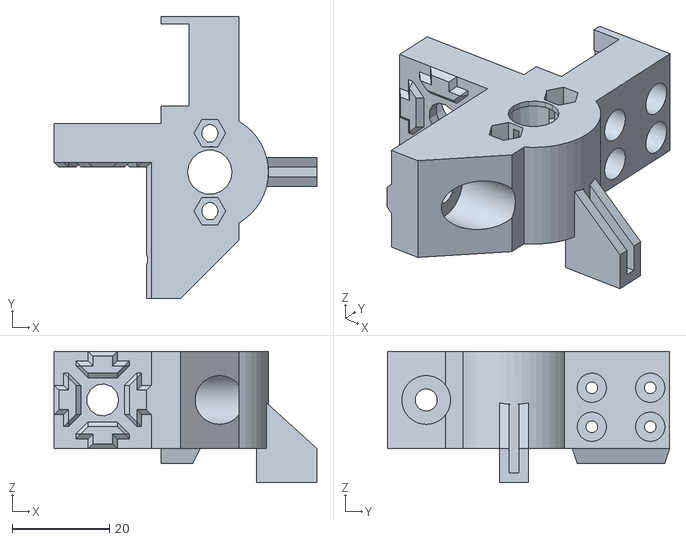
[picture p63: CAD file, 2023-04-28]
revB/stls/DIYLB_carriage_D.stl
54.0 x 58.0 x 27.0

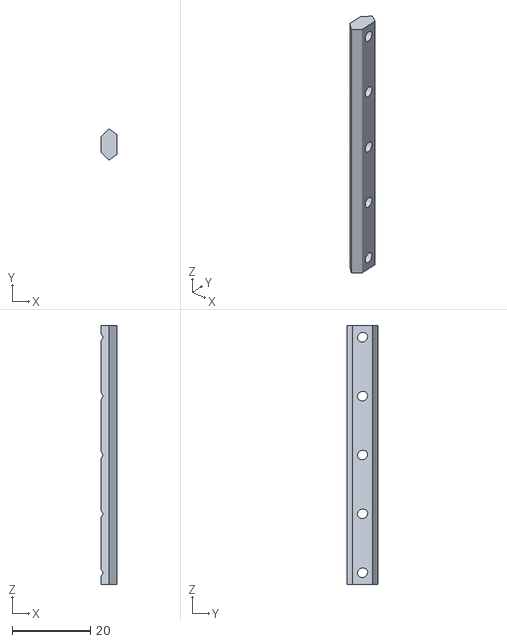
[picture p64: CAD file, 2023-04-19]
revB/stls/DIYLB_rail.stl
4.00 x 8.00 x 66.0

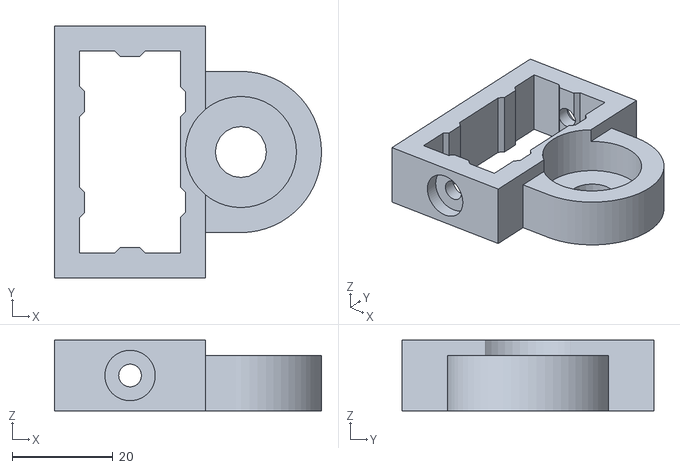
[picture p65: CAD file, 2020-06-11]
revB/stls/DIYLB_crank_bearing.stl
53.0 x 50.0 x 14.0

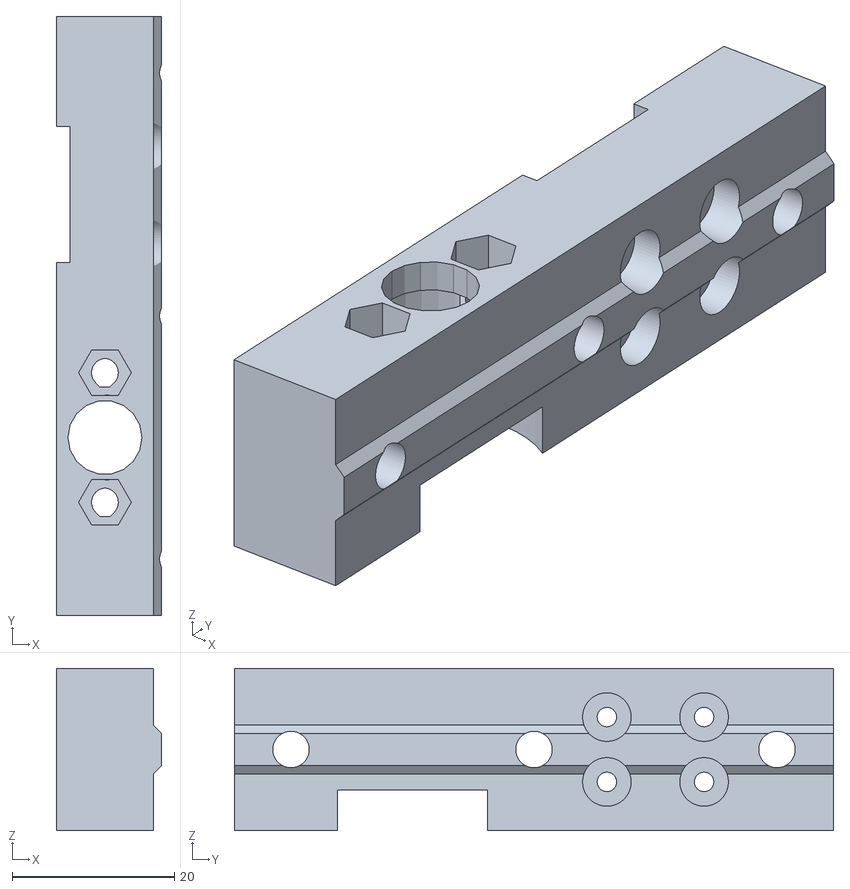
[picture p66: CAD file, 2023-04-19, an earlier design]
revA/stls/DIYLB_carriage_left.stl
13.0 x 74.0 x 20.0

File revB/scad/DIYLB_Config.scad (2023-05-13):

//###############################################################################
//# DIY Laser Bed - Configuration                                               #
//###############################################################################
//#    Copyright 2018 - 2019 Dirk Heisswolf                                     #
//#    This file is part of the DIY Laser Bed project.                          #
//#                                                                             #
//#    This project is free software: you can redistribute it and/or modify     #
//#    it under the terms of the GNU General Public License as published by     #
//#    the Free Software Foundation, either version 3 of the License, or        #
//#    (at your option) any later version.                                      #
//#                                                                             #
//#    This project is distributed in the hope that it will be useful,          #
//#    but WITHOUT ANY WARRANTY; without even the implied warranty of           #
//#    MERCHANTABILITY or FITNESS FOR A PARTICULAR PURPOSE.  See the            #
//#    GNU General Public License for more details.                             #
//#                                                                             #
//#    You should have received a copy of the GNU General Public License        #
//#    along with this project.  If not, see <http://www.gnu.org/licenses/>.    #
//#                                                                             #
//#    This project makes use of the NopSCADlib library                         #
//#    (see https://github.com/nophead/NopSCADlib).                             #
//#                                                                             #
//###############################################################################
//# Description:                                                                #
//#   Global configurations for the DIY Laser Bed.                              #
//#                                                                             #
//###############################################################################
//# Version History:                                                            #
//#   February 14, 2020                                                         #
//#      - Initial release                                                      #
//#                                                                             #
//#   May 13, 2020                                                              #
//#      - Added toothed idler                                                  #
//#                                                                             #
//###############################################################################
include <../../lib/NopSCADlib/lib.scad>
//include <../../lib/NopSCADlib/core.scad>
include <../../lib/NopSCADlib/vitamins/extrusions.scad>
include <../../lib/NopSCADlib/vitamins/screws.scad>
include <../../lib/NopSCADlib/vitamins/belts.scad>
include <../../lib/NopSCADlib/vitamins/pulleys.scad>
include <../../lib/NopSCADlib/vitamins/ball_bearings.scad>
include <../../lib/NopSCADlib/vitamins/rod.scad>
include <../../lib/NopSCADlib/vitamins/rails.scad>

//Ball bearings
//=============
//               n     b  d   h   c                             
//               a     o  i   e   o                             
//               m     r  a   i   l                             
//               e     e  m   g   o                             
//                        .   h   r                          
//                            t                             
//$bb_type   = ["608", 8, 22, 7, "OrangeRed", 1.4, 2.0]; //Standard 608 bearings
$bb_type     = BB608;                                    //Standard 608 bearings
$bb_height   = $bb_type[3];                              //Ball bearing height
$bb_diameter = $bb_type[2];                              //Ball bearing diameter

//Pulleys
//=======
//
//                                   n       t   o      b       w     h   h    b  f     f    s  s     s              s
//                                   a       e   d      e       i     u   u    o  l     l    c  c     c              c
//                                   m       e          l       d     b   b    r  a     a    r  r     r              r
//                                   e       t          t       t              e  n     n    e  e     e              e
//                                           h                  h     d   l       g     g    w  w     w              w
//                                                                                e     e                            s
//                                                                                           l  z     
//                                                                                d     t             
$i_type  = ["GT2x20_plain_idler",   "GT2",    0, 12.0,  GT2x6,  6.5,  18, 0,   5, 18.0, 1.0, 0, 0,    false,         0];
$ti_type = ["GT2x20_toothed_idler", "GT2",   20, 12.22, GT2x6,  6.5,  18, 0,   5, 18.0, 1.0, 0, 0,    false,         0];
$p_type  = ["GT2x20_pulley",        "GT2OB", 20, 12.22, GT2x6,  7.5,  16, 5.5, 8, 16.0, 1.0, 6, 3.25, M3_grub_screw, 2]; //Standarf GT2 T20 pulley
$p_hubl  = $p_type[7];                                                                                            //Length of the hub
$p_width = $p_type[4]; 

//Dimensions
//==========
$frame_depth = 295;

//Cent coin
//=========
//$cent_thickness = 1.67;
$cent_thickness = 1.9;
$cent_diameter  = 16.4;

//Magnet
//=========
$magnet_thickness = 4.5;
$magnet_diameter  = 19.8;

//Animation
//=========
//$t=0.5;
highest_pos = 70;
lowest_pos  = 27;
$elevation = lowest_pos + (highest_pos-lowest_pos) * 2 * abs($t-0.5);
$rotation  = 180 * (highest_pos-lowest_pos) * 2 * abs($t-0.5);
//$elevation = 30;
//$rotation  = 20;
$vpr = [70, 0, $t * 360];
$vpt = [150,150,30];
$vpd = 1000;

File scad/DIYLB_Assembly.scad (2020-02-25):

//###############################################################################
//# DIY Laser Bed - Main Assembly                                               #
//###############################################################################
//#    Copyright 2020 Dirk Heisswolf                                            #
//#    This file is part of the DIY Laser Bed project.                          #
//#                                                                             #
//#    This project is free software: you can redistribute it and/or modify     #
//#    it under the terms of the GNU General Public License as published by     #
//#    the Free Software Foundation, either version 3 of the License, or        #
//#    (at your option) any later version.                                      #
//#                                                                             #
//#    This project is distributed in the hope that it will be useful,          #
//#    but WITHOUT ANY WARRANTY; without even the implied warranty of           #
//#    MERCHANTABILITY or FITNESS FOR A PARTICULAR PURPOSE.  See the            #
//#    GNU General Public License for more details.                             #
//#                                                                             #
//#    You should have received a copy of the GNU General Public License        #
//#    along with this project.  If not, see <http://www.gnu.org/licenses/>.    #
//#                                                                             #
//#    This project makes use of the NopSCADlib library                         #
//#    (see https://github.com/nophead/NopSCADlib).                             #
//#                                                                             #
//###############################################################################
//# Description:                                                                #
//#   Assembly of the DIY Laser Bed.                                            #
//#                                                                             #
//###############################################################################
//# Version History:                                                            #
//#   February 13, 2020                                                         #
//#      - Initial release                                                      #
//#                                                                             #
//###############################################################################

//! This is a DIY laser bed for K40 cutters and clones. 

include <DIYLB_Config.scad>
use     <DIYLB_Base.scad>
use     <DIYLB_Crank.scad>
use     <DIYLB_Rail.scad>
use     <DIYLB_Bed.scad>

//Animation
//=========
//$elevation = 30 + ($t * 40);
//$rotation  =       $t * 360*20;
////$elevation = 70;
////$rotation  = 20;
//$vpr = [70, 0, $t * 360];
//$vpt = [150,150,0];
//$vpd = 1000;

$explode=1;
$vpr = [70, 0, 0];
$vpt = [150,150,0];



//Crank to Base
//==============
//! 1. Attach the crank holder to the base of the frame  
//! 2. Tighten the screws of the L-brackets
module DIYLB_CrankBase_assembly() {
    pose([60, 0, 5], [0,240,0])
    assembly("Crank Holder") {
    
    //Base
    DIYLB_Base_assembly();    

    //Base
    translate([0,130,0]) explode([-25,0,0]) DIYLB_Crank_assembly();    

    }
}

//Columns to Base
//===============
//! 1. Attach the for columns to the base of the frame  
//! 2. Tighten the screws of the L-brackets
module DIYLB_ColumnBase_assembly() {
    pose([70, 0, 0], [150,150,0])
    assembly("Columns") {
    
    //Base
    DIYLB_CrankBase_assembly();    

    //Columns
    translate([20,32,0])   mirror([0,0,0])                  explode(20) DIYLB_Rail_assembly();
    translate([340,32,0])  mirror([1,0,0])                  explode(20) DIYLB_Rail_assembly();
    translate([340,268,0]) mirror([1,0,0])  mirror([0,1,0]) explode(20) DIYLB_Rail_assembly();
    translate([20,268,0])  mirror([0,1,0])                  explode(20) DIYLB_Rail_assembly();

    }
}

//Bed to Columns
//==============
//! 1. Thread the assembled bed into the rails and rods of the Z-axis.
module DIYLB_ColumnBed_assembly() {
    pose([70, 0, 0], [150,150,0])
    assembly("Bed") {

        //Base and columns
        DIYLB_ColumnBase_assembly();
        
        //Bed    
        explode(100) DIYLB_Bed_assembly();
    }
}

//Top to Columns
//==============
//! 1. Attach the top extrusions to the rest of the frame.
module DIYLB_ColumnTop_assembly() {
    pose([70, 0, 0], [150,150,0])
    assembly("Top") {

    //Base
    DIYLB_ColumnBed_assembly();


    }
}

module main_assembly() {
    DIYLB_ColumnTop_assembly();
}


////Base framework
////==============
//use <DIYLB_Base.scad>
//DIYLB_Base();
//
////Lower Bearings
////==============
//use <DIYLB_LBearing.scad>
//translate([20,32,0])   mirror([0,0,0])                 DIYLB_LBearing(rotation=$rotation);
//translate([340,32,0])  mirror([1,0,0])                 DIYLB_LBearing(rotation=$rotation);
//translate([340,268,0]) mirror([1,0,0]) mirror([0,1,0]) DIYLB_LBearing(rotation=$rotation);
//translate([20,268,0])  mirror([0,1,0])                 DIYLB_LBearing(rotation=$rotation);
//p2=[32,72];
////translate([p2.x,p2.y,20]) cylinder(40,d=10);
//p3=[328,72];
////translate([p3.x,p3.y,20]) cylinder(40,d=10);
//p4=[328,228];
////translate([p4.x,p4.y,20]) cylinder(40,d=10);
//p5=[32,228];
////translate([p5.x,p5.y,20]) cylinder(40,d=10);
//
////Upper Bearings
////==============
//use <DIYLB_UBearing.scad>
//translate([20,32,0])   mirror([0,0,0])                 DIYLB_UBearing(rotation=$rotation);
//translate([340,32,0])  mirror([1,0,0])                 DIYLB_UBearing(rotation=$rotation);
//translate([340,268,0]) mirror([1,0,0]) mirror([0,1,0]) DIYLB_UBearing(rotation=$rotation);
//translate([20,268,0])  mirror([0,1,0])                 DIYLB_UBearing(rotation=$rotation);
//
////Carriages
////=========
//use <DIYLB_Carriage.scad>
//translate([20,32,0])   mirror([0,0,0])                 DIYLB_Carriage(elevation=$elevation);
//translate([340,32,0])  mirror([1,0,0])                 DIYLB_Carriage(elevation=$elevation);
//translate([340,268,0]) mirror([1,0,0]) mirror([0,1,0]) DIYLB_Carriage(elevation=$elevation);
//translate([20,268,0])  mirror([0,1,0])                 DIYLB_Carriage(elevation=$elevation);
//
////Columns
////=======
//use <DIYLB_Rail.scad>
//translate([20,32,0])   mirror([0,0,0])                  DIYLB_Rail();
//translate([340,32,0])  mirror([1,0,0])                  DIYLB_Rail();
//translate([340,268,0]) mirror([1,0,0])  mirror([0,1,0]) DIYLB_Rail();
//translate([20,268,0])  mirror([0,1,0])  DIYLB_Rail();
//
////Crank
////=====
//use <DIYLB_Crank.scad>
//translate([0,130,0]) DIYLB_Crank(rotation=$rotation);
//p0=[-58,150];
////translate([p0.x,p0.y,20]) cylinder(60,d=10);
//
////Moving Table
////============
//use <DIYLB_Table.scad>
//DIYLB_Table(elevation=$elevation);
//
////Top Beams
////=========
//use <DIYLB_Top.scad>
//DIYLB_Top();
//
////Timing belt
////===========
//use <T-Nut.scad>
//translate([10,140,20]) rotate([0,0,270]) tnut(10);
//translate([10,140,20]) pulley(GT2x20_plain_idler);
//translate([10,160,20]) rotate([0,0,90])  tnut(10);
//translate([10,160,20]) pulley(GT2x20_plain_idler);
////p1=[10,76];
//p1=[10,140.5];
////translate([p1.x,p1.y,20]) cylinder(20,d=10);
////p6=[10,224];
//p6=[10,159.5];
////translate([p6.x,p6.y,20]) cylinder(20,d=10);
//
//belt_path = [[p6.x, p6.y, -pulley_pr(GT2x20_plain_idler)],
//             [p5.x, p5.y,  pulley_pr(GT2x20ob_pulley)],
//             [p4.x, p4.y,  pulley_pr(GT2x20ob_pulley)],
//             [p3.x, p3.y,  pulley_pr(GT2x20ob_pulley)],            
//             [p2.x, p2.y,  pulley_pr(GT2x20ob_pulley)],
//             [p1.x, p1.y, -pulley_pr(GT2x20_plain_idler)],
//             [p0.x, p0.y,  pulley_pr(GT2x20ob_pulley)]];
//
//belt = GT2x6;
//translate([0,0,24]) belt(belt, belt_path);
//        
//echo(Belt_length=belt_length(belt_path));

if($preview)
    main_assembly();

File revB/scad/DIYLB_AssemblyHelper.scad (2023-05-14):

//###############################################################################
//# DIY Laser Bed - Assembly Helper                                             #
//###############################################################################
//#    Copyright 2018 - 2023 Dirk Heisswolf                                     #
//#    This file is part of the DIY Laser Bed project.                          #
//#                                                                             #
//#    This project is free software: you can redistribute it and/or modify     #
//#    it under the terms of the GNU General Public License as published by     #
//#    the Free Software Foundation, either version 3 of the License, or        #
//#    (at your option) any later version.                                      #
//#                                                                             #
//#    This project is distributed in the hope that it will be useful,          #
//#    but WITHOUT ANY WARRANTY; without even the implied warranty of           #
//#    MERCHANTABILITY or FITNESS FOR A PARTICULAR PURPOSE.  See the            #
//#    GNU General Public License for more details.                             #
//#                                                                             #
//#    You should have received a copy of the GNU General Public License        #
//#    along with this project.  If not, see <http://www.gnu.org/licenses/>.    #
//#                                                                             #
//#    This project makes use of the NopSCADlib library                         #
//#    (see https://github.com/nophead/NopSCADlib).                             #
//#                                                                             #
//###############################################################################
//# Description:                                                                #
//#   Holds up the beams at an equal height to ajust the belt                   #
//#                                                                             #
//###############################################################################
//# Version History:                                                            #
//#   May 13, 2022                                                              #
//#      - Initial release                                                      #
//#                                                                             #
//###############################################################################
include <DIYLB_Config.scad>

//$explode = 1;
//$vpr = [70, 0, 25];
//$vpt = [0,0,50];


module miniMagnet() {
    description = str("Neodym Magnet (5mmx5mmx2mm)");
    vitamin(str("miniMagnet(): ", description));
    
    *color("Silver"){ cube([2,5,5]); }    
    color("Silver"){ cylinder(h=1,d=4); }    
}

module DIYLB_assemblyHelper_stl() {
    stl("DIYLB_assemblyHelper");   

    color(pp1_colour)
    difference() {
        union() {
           translate([-8,0,-4]) cube([10,10,58]);
        }    
        union() {
           translate([-20,-10,-19.8]) cube([20,40,20]);
           translate([-20,-10,49.8])  cube([20,40,20]);
           translate([-12,-10,2])  rotate([0,105,0]) cube([10,40,10]);
           translate([-12,-10,48]) rotate([0,-15,0]) cube([10,40,10]);
           hull() {
              translate([-30,10,4]) cube([40,40,42]);
              translate([-30,4,10]) cube([40,40,30]);
          }
          //Magnet inserts
         translate([-3,0.2,10]) rotate([270,0,0]) cylinder(h=1.2,d=4.2,$fn=12);
         translate([-3,0.2,25]) rotate([270,0,0]) cylinder(h=1.2,d=4.2,$fn=12);
         translate([-3,0.2,40]) rotate([270,0,0]) cylinder(h=1.2,d=4.2,$fn=12);
       }
    }    
}
DIYLB_assemblyHelper_stl();

//! 1. Insert the magnets during print.
module DIYLB_assemblyHelper_assembly () {
    pose([70, 0, 25],[0, 0, 50])
    assembly("DIYLB_assemblyHelper") {

        //Assembly helper
        DIYLB_assemblyHelper_stl();

        //Magnets
        explode([0,-10,0]) translate([-3,0.2,10]) rotate([270,0,0]) miniMagnet();
        explode([0,-10,0]) translate([-3,0.2,25]) rotate([270,0,0]) miniMagnet();
        explode([0,-10,0]) translate([-3,0.2,40]) rotate([270,0,0]) miniMagnet();
    }
}

if ($preview) {
    //$explode = 1;

    //Demo assembly
    DIYLB_assemblyHelper_assembly();

    //Demo extrusions
    translate([-10,-30,-10])  rotate([-90,0,0]) extrusion(E2020, 80, center=false);
    translate([-10,-30,60])  rotate([-90,0,00]) extrusion(E2020, 80, center=false);
}

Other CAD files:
revB/stls/DIYLB_top_A.stl
revB/stls/DIYLB_carriage_B.stl
revB/stls/DIYLB_top_front.stl
revB/stls/DIYLB_carriage_A.stl
revA/stls/DIYLB_carriage_right.stl
revB/scad/DIYLB.scad
revA/scad/DIYLB_Carriage.scad
revA/stls/DIYLB_lower_bearing.stl
revA/stls/DIYLB_upper_bearing.stl
revB/scad/DIYLB_Base.scad
revB/scad/DIYLB_Bed.scad
revB/scad/DIYLB_Carriage.scad
revB/scad/DIYLB_Crank.scad
revB/scad/DIYLB_Idler.scad
revB/scad/DIYLB_LBearing.scad
revB/scad/DIYLB_Magnet.scad
revB/scad/DIYLB_Rail.scad
revB/scad/DIYLB_Top.scad
revB/scad/DIYLB_UBearing.scad
revB/scad/vitamins/Cent.scad
revB/scad/vitamins/Crank.scad
revB/scad/vitamins/FlatSection.scad
revB/scad/vitamins/L-Bracket.scad
revB/scad/vitamins/Magnet.scad
revB/scad/vitamins/T-Nut.scad
revB/scad/vitamins/T8Lock.scad
revB/scad/vitamins/T8Nut.scad

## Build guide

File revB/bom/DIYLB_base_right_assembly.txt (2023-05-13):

DIYLB_base_right_assembly:
Vitamins:
  1 Extrusion E2020 x 300mm
  2 L-Bracket (20x20)
  4 Screw M3 grub x  6mm

Assemblies:
  1 DIYLB_idler_assembly
  2 DIYLB_lower_bearing_assemblies

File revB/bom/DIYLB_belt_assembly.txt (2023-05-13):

DIYLB_belt_assembly:
Vitamins:
  1 Belt GT2 x 6mm x 1222mm

Assemblies:
  1 DIYLB_top_to_columns_assembly

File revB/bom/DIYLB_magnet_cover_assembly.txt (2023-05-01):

DIYLB_magnet_cover_assemblies:
Vitamins:
  4 Euro-Cent coin

Printed:
  4 DIYLB_magnet_cover.stl

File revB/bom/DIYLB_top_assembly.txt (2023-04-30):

DIYLB_top_assemblies:
Vitamins:
  4 Screw M6 cap x 20mm
  4 Washer  M6 x 12.5mm x 1.5mm

Printed:
  2 DIYLB_top_A.stl
  2 DIYLB_top_B.stl

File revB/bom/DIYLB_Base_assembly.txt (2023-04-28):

DIYLB_Base_assembly:

Assemblies:
  2 DIYLB_base_center_assemblies
  1 DIYLB_base_left_assembly
  1 DIYLB_base_right_assembly

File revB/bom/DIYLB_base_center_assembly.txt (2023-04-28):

DIYLB_base_center_assemblies:
Vitamins:
  2 Extrusion E2020 x 320mm

Assemblies:
  4 DIYLB_magnet_assemblies

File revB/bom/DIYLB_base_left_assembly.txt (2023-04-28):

DIYLB_base_left_assembly:
Vitamins:
  1 Extrusion E2020 x 300mm
  4 L-Bracket (20x20)
  8 Screw M3 grub x  6mm

Assemblies:
  2 DIYLB_lower_bearing_assemblies

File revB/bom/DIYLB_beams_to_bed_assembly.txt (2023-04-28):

DIYLB_beams_to_bed_assembly:
Vitamins:
  1 Flat section 15mmx2mm, 272mm
  4 Flat section 15mmx2mm, 316mm

Printed:
  8 DIYLB_beam_holder.stl

Assemblies:
  1 DIYLB_bed_to_columns_assembly

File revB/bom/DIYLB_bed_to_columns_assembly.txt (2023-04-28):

DIYLB_bed_to_columns_assembly:

Assemblies:
  2 DIYLB_carriage_AB_assemblies
  1 DIYLB_columns_to_base_assembly

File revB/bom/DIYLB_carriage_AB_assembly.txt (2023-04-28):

DIYLB_carriage_AB_assemblies:
Vitamins:
  2 Extrusion E2020 x 235mm

Assemblies:
  1 DIYLB_carriage_A_assembly
  1 DIYLB_carriage_B_assembly
  1 DIYLB_carriage_C_assembly
  1 DIYLB_carriage_D_assembly

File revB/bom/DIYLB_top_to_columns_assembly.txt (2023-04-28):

DIYLB_top_to_columns_assembly:

Assemblies:
  1 DIYLB_beams_to_bed_assembly
  2 DIYLB_top_assemblies

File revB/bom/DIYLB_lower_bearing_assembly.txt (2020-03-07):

DIYLB_lower_bearing_assemblies:
Vitamins:
  4 Ball bearing 608-2RS 8mm x 22mm x 7mm
  4 Euro-Cent coin
  4 Pulley GT2OB 20 teeth
  8 Screw M3 grub x  6mm
  8 Screw M4 cap x 12mm
  4 Threaded rod M8 x 100mm
  8 T-Nut (20x20)
  8 Washer  M4 x 9mm x 0.8mm

Printed:
  4 DIYLB_lower_bearing.stl

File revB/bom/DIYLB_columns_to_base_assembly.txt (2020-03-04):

DIYLB_columns_to_base_assembly:

Assemblies:
  1 DIYLB_crank_to_base_assembly
  4 DIYLB_rail_assemblies

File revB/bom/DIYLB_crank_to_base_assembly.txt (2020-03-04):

DIYLB_crank_to_base_assembly:

Assemblies:
  1 DIYLB_Base_assembly
  1 DIYLB_crank_assembly

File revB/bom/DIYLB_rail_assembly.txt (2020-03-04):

DIYLB_rail_assemblies:
Vitamins:
  4 Extrusion E2020 x 70mm
 20 Nut M2 x 1.6mm 
  4 Linear rail MGN7 x 70mm
 20 Screw M2 cap x  6mm

Printed:
  4 DIYLB_rail.stl

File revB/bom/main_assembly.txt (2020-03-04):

main_assembly:

Assemblies:
  1 DIYLB_belt_assembly

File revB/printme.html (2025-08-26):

# RevB

This is a DIY laser bed for K40 cutters and clones. inside

## Table of Contents

1. Parts list
2. DIYLB Top Assembly
3. DIYLB Carriage D Assembly
4. DIYLB Carriage C Assembly
5. DIYLB Carriage AB Assembly
6. DIYLB Carriage B Assembly
7. DIYLB Carriage A Assembly
8. DIYLB Rail Assembly
9. DIYLB Crank Assembly
10. DIYLB Idler Assembly
11. DIYLB Lower Bearing Assembly
12. DIYLB Base Right Assembly
13. DIYLB Magnet Cover Assembly
14. DIYLB Magnet Assembly
15. DIYLB Base Center Assembly
16. DIYLB Base Left Assembly
17. DIYLB Base Assembly
18. DIYLB Crank To Base Assembly
19. DIYLB Columns To Base Assembly
20. DIYLB Bed To Columns Assembly
21. DIYLB Beams To Bed Assembly
22. DIYLB Top To Columns Assembly
23. DIYLB Belt Assembly

## Parts list

2 x DIYLB Top | DIYLB Carriage D | DIYLB Carriage C | 2 x DIYLB Carriage AB | DIYLB Carriage B | DIYLB Carriage A | 4 x DIYLB Rail | DIYLB Crank | DIYLB Idler | 4 x DIYLB Lower Bearing | DIYLB Base Right | 4 x DIYLB Magnet Cover | 4 x DIYLB Magnet | 2 x DIYLB Base Center | DIYLB Base Left | DIYLB Base | DIYLB Crank To Base | DIYLB Columns To Base | DIYLB Bed To Columns | DIYLB Beams To Bed | DIYLB Top To Columns | DIYLB Belt | TOTALS
| | | | | | | | | | | | | | | | | | | | | | | Vitamins
. | . | . | . | . | . | . | 2 | . | 4 | . | . | . | . | . | . | . | . | . | . | . | . | 6 | Ball bearing 608-2RS 8mm x 22mm x 7mm
. | . | . | . | . | . | . | . | . | . | . | . | . | . | . | . | . | . | . | . | . | 1 | 1 | Belt GT2 x 6mm x 1222mm
. | . | . | . | . | . | . | . | . | 4 | . | 4 | . | . | . | . | . | . | . | . | . | . | 8 | Euro-Cent coin
. | . | . | 2 | . | . | . | . | . | . | . | . | . | . | . | . | . | . | . | . | . | . | 2 | Extrusion E2020 x 235mm
. | . | . | . | . | . | . | . | . | . | 1 | . | . | . | 1 | . | . | . | . | . | . | . | 2 | Extrusion E2020 x 300mm
. | . | . | . | . | . | . | . | . | . | . | . | . | 2 | . | . | . | . | . | . | . | . | 2 | Extrusion E2020 x 320mm
. | . | . | . | . | . | 4 | . | . | . | . | . | . | . | . | . | . | . | . | . | . | . | 4 | Extrusion E2020 x 70mm
. | . | . | . | . | . | . | 1 | . | . | . | . | . | . | . | . | . | . | . | . | . | . | 1 | Extrusion E2040 x 60mm
. | . | . | . | . | . | . | 1 | . | . | . | . | . | . | . | . | . | . | . | . | . | . | 1 | Extrusion E2040 x 70mm
. | . | . | . | . | . | . | . | . | . | . | . | . | . | . | . | . | . | . | 1 | . | . | 1 | Flat section 15mmx2mm, 272mm
. | . | . | . | . | . | . | . | . | . | . | . | . | . | . | . | . | . | . | 4 | . | . | 4 | Flat section 15mmx2mm, 316mm
. | . | . | . | . | . | . | 2 | . | . | 2 | . | . | . | 4 | . | . | . | . | . | . | . | 8 | L-Bracket (20x20)
. | . | . | . | . | . | 4 | . | . | . | . | . | . | . | . | . | . | . | . | . | . | . | 4 | Linear rail MGN7 x 70mm
. | 1 | 1 | . | 1 | 1 | . | . | . | . | . | . | . | . | . | . | . | . | . | . | . | . | 4 | Linear rail carriage MGN7C
. | . | . | . | . | . | . | . | . | . | . | . | 4 | . | . | . | . | . | . | . | . | . | 4 | Neodym Magnet (D=20,H=4.5)
. | . | . | . | . | . | 20 | . | . | . | . | . | . | . | . | . | . | . | . | . | . | . | 20 | Nut M2 x 1.6mm
. | 2 | 2 | . | 2 | 2 | . | . | . | . | . | . | . | . | . | . | . | . | . | . | . | . | 8 | Nut M3 x 2.4mm
. | . | . | . | . | . | . | . | 1 | . | . | . | . | . | . | . | . | . | . | . | . | . | 1 | Nut M5 x 4mm
. | . | . | . | . | . | . | 1 | . | . | . | . | . | . | . | . | . | . | . | . | . | . | 1 | Nut M8 x 6.5mm
. | . | . | . | . | . | . | . | 1 | . | . | . | . | . | . | . | . | . | . | . | . | . | 1 | Pulley GT2 idler 20 teeth
. | . | . | . | . | . | . | 2 | . | . | . | . | . | . | . | . | . | . | . | . | . | . | 2 | Pulley GT2 idler smooth 12mm
. | . | . | . | . | . | . | 1 | . | 4 | . | . | . | . | . | . | . | . | . | . | . | . | 5 | Pulley GT2OB 20 teeth
. | . | . | . | . | . | 20 | . | . | . | . | . | . | . | . | . | . | . | . | . | . | . | 20 | Screw M2 cap x 6mm
. | 4 | 4 | . | 4 | 4 | . | . | . | . | . | . | . | . | . | . | . | . | . | . | . | . | 16 | Screw M2 cap x 10mm
. | . | . | . | . | . | . | 6 | . | 8 | 4 | . | . | . | 8 | . | . | . | . | . | . | . | 26 | Screw M3 grub x 6mm
. | 2 | 2 | . | 2 | 2 | . | . | . | . | . | . | . | . | . | . | . | . | . | . | . | . | 8 | Screw M3 pan x 12mm
. | 1 | 1 | . | 1 | 1 | . | . | 2 | 8 | . | . | 8 | . | . | . | . | . | . | . | . | . | 22 | Screw M4 cap x 12mm
. | . | . | . | . | . | . | 2 | . | . | . | . | . | . | . | . | . | . | . | . | . | . | 2 | Screw M4 cap x 15mm
. | . | . | . | . | . | . | 4 | . | . | . | . | . | . | . | . | . | . | . | . | . | . | 4 | Screw M4 dome x 8mm
. | . | . | . | . | . | . | . | 1 | . | . | . | . | . | . | . | . | . | . | . | . | . | 1 | Screw M5 cap x 28mm
4 | . | . | . | . | . | . | . | . | . | . | . | . | . | . | . | . | . | . | . | . | . | 4 | Screw M6 cap x 20mm
. | 1 | 1 | . | 1 | 1 | . | . | . | . | . | . | . | . | . | . | . | . | . | . | . | . | 4 | Screw M6 pan x 20mm
. | . | . | . | . | . | . | 3 | . | . | . | . | . | . | . | . | . | . | . | . | . | . | 3 | Screw M8 hex x 50mm
. | 1 | 1 | . | 1 | 1 | . | . | 2 | 8 | . | . | 8 | . | . | . | . | . | . | . | . | . | 22 | T-Nut (20x20)
. | . | . | . | . | . | . | 4 | . | . | . | . | . | . | . | . | . | . | . | . | . | . | 4 | T-Nut (20x20)
. | . | . | . | . | . | . | 2 | . | . | . | . | . | . | . | . | . | . | . | . | . | . | 2 | T-Nut (20x20)
. | 1 | 1 | . | 1 | 1 | . | . | . | . | . | . | . | . | . | . | . | . | . | . | . | . | 4 | T8-Nut (narrow)
. | . | . | . | . | . | . | . | . | 4 | . | . | . | . | . | . | . | . | . | . | . | . | 4 | Threaded rod M8 x 100mm
. | 4 | 4 | . | 4 | 4 | . | . | . | . | . | . | . | . | . | . | . | . | . | . | . | . | 16 | Washer M2 x 5mm x 0.3mm
. | 1 | 1 | . | 1 | 1 | . | 6 | 2 | 8 | . | . | 8 | . | . | . | . | . | . | . | . | . | 28 | Washer M4 x 9mm x 0.8mm
. | . | . | . | . | . | . | . | 1 | . | . | . | . | . | . | . | . | . | . | . | . | . | 1 | Washer M5 x 10mm x 1mm
4 | 1 | 1 | . | 1 | 1 | . | . | . | . | . | . | . | . | . | . | . | . | . | . | . | . | 8 | Washer M6 x 12.5mm x 1.5mm
8 | 19 | 19 | 2 | 19 | 19 | 48 | 37 | 10 | 48 | 7 | 4 | 28 | 2 | 13 | . | . | . | . | 5 | . | 1 | 289 | Total vitamins count
| | | | | | | | | | | | | | | | | | | | | | | 3D printed parts
. | . | . | . | . | . | . | . | . | . | . | . | . | . | . | . | . | . | . | 8 | . | . | 8 | DIYLB_beam_holder.stl
. | . | . | . | . | 1 | . | . | . | . | . | . | . | . | . | . | . | . | . | . | . | . | 1 | DIYLB_carriage_A.stl
. | . | . | . | 1 | . | . | . | . | . | . | . | . | . | . | . | . | . | . | . | . | . | 1 | DIYLB_carriage_B.stl
. | . | 1 | . | . | . | . | . | . | . | . | . | . | . | . | . | . | . | . | . | . | . | 1 | DIYLB_carriage_C.stl
. | 1 | . | . | . | . | . | . | . | . | . | . | . | . | . | . | . | . | . | . | . | . | 1 | DIYLB_carriage_D.stl
. | . | . | . | . | . | . | 1 | . | . | . | . | . | . | . | . | . | . | . | . | . | . | 1 | DIYLB_crank.stl
. | . | . | . | . | . | . | 2 | . | . | . | . | . | . | . | . | . | . | . | . | . | . | 2 | DIYLB_crank_bearing.stl
. | . | . | . | . | . | . | . | 1 | . | . | . | . | . | . | . | . | . | . | . | . | . | 1 | DIYLB_idler.stl
. | . | . | . | . | . | . | . | . | 4 | . | . | . | . | . | . | . | . | . | . | . | . | 4 | DIYLB_lower_bearing.stl
. | . | . | . | . | . | . | . | . | . | . | . | 4 | . | . | . | . | . | . | . | . | . | 4 | DIYLB_magnet.stl
. | . | . | . | . | . | . | . | . | . | . | 4 | . | . | . | . | . | . | . | . | . | . | 4 | DIYLB_magnet_cover.stl
. | . | . | . | . | . | 4 | . | . | . | . | . | . | . | . | . | . | . | . | . | . | . | 4 | DIYLB_rail.stl
2 | . | . | . | . | . | . | . | . | . | . | . | . | . | . | . | . | . | . | . | . | . | 2 | DIYLB_top_A.stl
2 | . | . | . | . | . | . | . | . | . | . | . | . | . | . | . | . | . | . | . | . | . | 2 | DIYLB_top_B.stl
4 | 1 | 1 | . | 1 | 1 | 4 | 3 | 1 | 4 | . | 4 | 4 | . | . | . | . | . | . | 8 | . | . | 36 | Total 3D printed parts count

## 2 x DIYLB Top Assembly

### Vitamins

Qty | Description
4 | Screw M6 cap x 20mm
4 | Washer M6 x 12.5mm x 1.5mm

### 3D Printed parts

2 x DIYLB_top_A.stl | 2 x DIYLB_top_B.stl
DIYLB_top_A.stl | DIYLB_top_B.stl

### Assembly instructions

DIYLB_top_assembly

1. Cut a M6 thread into the top of the vertical 20x20 extrusions
2. Attach the top holders
3. Secure the top holders with M6 screws

DIYLB_top_assembled

## DIYLB Carriage D Assembly

### Vitamins

Qty | Description
1 | Linear rail carriage MGN7C
2 | Nut M3 x 2.4mm
4 | Screw M2 cap x 10mm
2 | Screw M3 pan x 12mm
1 | Screw M4 cap x 12mm
1 | Screw M6 pan x 20mm
1 | T-Nut (20x20)
1 | T8-Nut (narrow)
4 | Washer M2 x 5mm x 0.3mm
1 | Washer M4 x 9mm x 0.8mm
1 | Washer M6 x 12.5mm x 1.5mm

### 3D Printed parts

1 x DIYLB_carriage_D.stl

DIYLB_carriage_D.stl

### Assembly instructions

DIYLB_carriage_D_assembly

1. Attatch T8-nut to the carriage holder, using M3 screws,
2. Attatch the rail carriage to the carriage holder using M2 screws.
3. Put a T-nuts into the mounting hole.

DIYLB_carriage_D_assembled

## DIYLB Carriage C Assembly

### Vitamins

Qty | Description
1 | Linear rail carriage MGN7C
2 | Nut M3 x 2.4mm
4 | Screw M2 cap x 10mm
2 | Screw M3 pan x 12mm
1 | Screw M4 cap x 12mm
1 | Screw M6 pan x 20mm
1 | T-Nut (20x20)
1 | T8-Nut (narrow)
4 | Washer M2 x 5mm x 0.3mm
1 | Washer M4 x 9mm x 0.8mm
1 | Washer M6 x 12.5mm x 1.5mm

### 3D Printed parts

1 x DIYLB_carriage_C.stl

DIYLB_carriage_C.stl

### Assembly instructions

DIYLB_carriage_C_assembly

1. Attatch T8-nut to the carriage holder, using M3 screws,
2. Attatch the rail carriage to the carriage holder using M2 screws.
3. Put a T-nuts into the mounting hole.

DIYLB_carriage_C_assembled

## 2 x DIYLB Carriage AB Assembly

### Vitamins

Qty | Description
2 | Extrusion E2020 x 235mm

### Sub-assemblies

1 x DIYLB_carriage_A_assembly | 1 x DIYLB_carriage_B_assembly | 1 x DIYLB_carriage_C_assembly
DIYLB_carriage_A_assembled | DIYLB_carriage_B_assembled | DIYLB_carriage_C_assembled

1 x DIYLB_carriage_D_assembly

DIYLB_carriage_D_assembled

### Assembly instructions

DIYLB_carriage_AB_assembly

1. Cut a M6 thread into both ends of the extrusion,
2. Attatch attxh the carriage holders

DIYLB_carriage_AB_assembled

## DIYLB Carriage B Assembly

### Vitamins

Qty | Description
1 | Linear rail carriage MGN7C
2 | Nut M3 x 2.4mm
4 | Screw M2 cap x 10mm
2 | Screw M3 pan x 12mm
1 | Screw M4 cap x 12mm
1 | Screw M6 pan x 20mm
1 | T-Nut (20x20)
1 | T8-Nut (narrow)
4 | Washer M2 x 5mm x 0.3mm
1 | Washer M4 x 9mm x 0.8mm
1 | Washer M6 x 12.5mm x 1.5mm

### 3D Printed parts

1 x DIYLB_carriage_B.stl

DIYLB_carriage_B.stl

### Assembly instructions

DIYLB_carriage_B_assembly

1. Attatch T8-nut to the carriage holder, using M3 screws,
2. Attatch the rail carriage to the carriage holder using M2 screws.
3. Put a T-nuts into the mounting hole.

DIYLB_carriage_B_assembled

## DIYLB Carriage A Assembly

### Vitamins

Qty | Description
1 | Linear rail carriage MGN7C
2 | Nut M3 x 2.4mm
4 | Screw M2 cap x 10mm
2 | Screw M3 pan x 12mm
1 | Screw M4 cap x 12mm
1 | Screw M6 pan x 20mm
1 | T-Nut (20x20)
1 | T8-Nut (narrow)
4 | Washer M2 x 5mm x 0.3mm
1 | Washer M4 x 9mm x 0.8mm
1 | Washer M6 x 12.5mm x 1.5mm

### 3D Printed parts

1 x DIYLB_carriage_A.stl

DIYLB_carriage_A.stl

### Assembly instructions

DIYLB_carriage_A_assembly

1. Attatch T8-nut to the carriage holder, using M3 screws,
2. Attatch the rail carriage to the carriage holder using M2 screws.
3. Put a T-nuts into the mounting hole.

DIYLB_carriage_A_assembled

## 4 x DIYLB Rail Assembly

### Vitamins

Qty | Description
4 | Extrusion E2020 x 70mm
4 | Linear rail MGN7 x 70mm
20 | Nut M2 x 1.6mm
20 | Screw M2 cap x 6mm

### 3D Printed parts

4 x DIYLB_rail.stl

DIYLB_rail.stl

### Assembly instructions

DIYLB_rail_assembly

1. Insert the M2 nuts into the printed holder.
2. Attach the rail loosely.
3. Slide the printed holder into the 20x20 extrusion and tighten the screws.

DIYLB_rail_assembled

## DIYLB Crank Assembly

### Vitamins

Qty | Description
2 | Ball bearing 608-2RS 8mm x 22mm x 7mm
1 | Extrusion E2040 x 60mm
1 | Extrusion E2040 x 70mm
2 | L-Bracket (20x20)
1 | Nut M8 x 6.5mm
2 | Pulley GT2 idler smooth 12mm
1 | Pulley GT2OB 20 teeth
6 | Screw M3 grub x 6mm
2 | Screw M4 cap x 15mm
4 | Screw M4 dome x 8mm
3 | Screw M8 hex x 50mm
4 | T-Nut (20x20)
2 | T-Nut (20x20)
6 | Washer M4 x 9mm x 0.8mm

### 3D Printed parts

1 x DIYLB_crank.stl | 2 x DIYLB_crank_bearing.stl
DIYLB_crank.stl | DIYLB_crank_bearing.stl

### Assembly instructions

DIYLB_crank_assembly

1. Connect the two 20x40 extrusions with L-brackets.
2. Assemble the axis as illustrated.
3. Slide the printed holders over the vertical 20x40 extrusion (and loosely insert the timing belt).
4. Move the two printed holders as far apart as possible and tighten the screws.
5. Slide two idlers on T-nuts onto the top slot of the horizontal 20x40 extrusion.

DIYLB_crank_assembled

## DIYLB Idler Assembly

### Vitamins

Qty | Description
1 | Nut M5 x 4mm
1 | Pulley GT2 idler 20 teeth
2 | Screw M4 cap x 12mm
1 | Screw M5 cap x 28mm
2 | T-Nut (20x20)
2 | Washer M4 x 9mm x 0.8mm
1 | Washer M5 x 10mm x 1mm

### 3D Printed parts

1 x DIYLB_idler.stl

DIYLB_idler.stl

### Assembly instructions

DIYLB_idler_assembly

1. Screw the idler onto the holder.
2. Attach two T-nuts with screws and washers.

DIYLB_idler_assembled

## 4 x DIYLB Lower Bearing Assembly

### Vitamins

Qty | Description
4 | Ball bearing 608-2RS 8mm x 22mm x 7mm
4 | Euro-Cent coin
4 | Pulley GT2OB 20 teeth
8 | Screw M3 grub x 6mm
8 | Screw M4 cap x 12mm
8 | T-Nut (20x20)
4 | Threaded rod M8 x 100mm
8 | Washer M4 x 9mm x 0.8mm

### 3D Printed parts

4 x DIYLB_lower_bearing.stl

DIYLB_lower_bearing.stl

### Assembly instructions

DIYLB_lower_bearing_assembly

1. Put a EuroCent coin in the bottom of the lower ball bearing holder.
2. Squeze the ball bearing into the holder.
3. Attach two T-nuts with screws and washers.
4. Put the pulley loosely onto the threaded rod and insert them into the ball bearingpulles.

DIYLB_lower_bearing_assembled

## DIYLB Base Right Assembly

### Vitamins

Qty | Description
1 | Extrusion E2020 x 300mm
2 | L-Bracket (20x20)
4 | Screw M3 grub x 6mm

### Sub-assemblies

1 x DIYLB_idler_assembly | 2 x DIYLB_lower_bearing_assembly
DIYLB_idler_assembled | DIYLB_lower_bearing_assembled

### Assembly instructions

DIYLB_base_right_assembly

1. Slide two L-brackets onto the top slot of the 20x20 extrusion.
2. Slide the two holders for the ball bearings onto the lef-thand slot of the 20x20 extrusion.
3. Attach the idler mount

DIYLB_base_right_assembled

## 4 x DIYLB Magnet Cover Assembly

### Vitamins

Qty | Description
4 | Euro-Cent coin

### 3D Printed parts

4 x DIYLB_magnet_cover.stl

DIYLB_magnet_cover.stl

### Assembly instructions

DIYLB_magnet_cover_assembly

1. insert cent coin during print.

DIYLB_magnet_cover_assembled

## 4 x DIYLB Magnet Assembly

### Vitamins

Qty | Description
4 | Neodym Magnet (D=20,H=4.5)
8 | Screw M4 cap x 12mm
8 | T-Nut (20x20)
8 | Washer M4 x 9mm x 0.8mm

### 3D Printed parts

4 x DIYLB_magnet.stl

DIYLB_magnet.stl

### Sub-assemblies

4 x DIYLB_magnet_cover_assembly

DIYLB_magnet_cover_assembled

### Assembly instructions

DIYLB_magnet_assembly

1. Squeze the magnet into the holder.
2. Attach two T-nuts with screws and washers.
3. Put the covers on top of the magnets.

DIYLB_magnet_assembled

## 2 x DIYLB Base Center Assembly

### Vitamins

Qty | Description
2 | Extrusion E2020 x 320mm

### Sub-assemblies

4 x DIYLB_magnet_assembly

DIYLB_magnet_assembled

### Assembly instructions

DIYLB_base_center_assembly

1. Attach two magnet holders to the 320mm 20x20 extrusion.

DIYLB_base_center_assembled

## DIYLB Base Left Assembly

### Vitamins

Qty | Description
1 | Extrusion E2020 x 300mm
4 | L-Bracket (20x20)
8 | Screw M3 grub x 6mm

### Sub-assemblies

2 x DIYLB_lower_bearing_assembly

DIYLB_lower_bearing_assembled

### Assembly instructions

DIYLB_base_left_assembly

1. Slide two L-brackets onto the top slot of the 20x20 extrusion.
2. Slide the two holders for the ball bearings onto the right-hand slot of the 20x20 extrusion.
3. Slide two L-brackets onto the left-hand slot of the 20x20 extrusion.

DIYLB_base_left_assembled

## DIYLB Base Assembly

### Sub-assemblies

2 x DIYLB_base_center_assembly | 1 x DIYLB_base_left_assembly | 1 x DIYLB_base_right_assembly
DIYLB_base_center_assembled | DIYLB_base_left_assembled | DIYLB_base_right_assembled

### Assembly instructions

DIYLB_Base_assembly

1. Attach all parts of the base frame
2. Tighten the screws of the bearing holders, connecting 20x20 extrusions

DIYLB_Base_assembled

## DIYLB Crank To Base Assembly

### Sub-assemblies

1 x DIYLB_Base_assembly | 1 x DIYLB_crank_assembly
DIYLB_Base_assembled | DIYLB_crank_assembled

### Assembly instructions

DIYLB_crank_to_base_assembly

1. Attach the crank holder to the base of the frame
2. Tighten the screws of the L-brackets

DIYLB_crank_to_base_assembled

## DIYLB Columns To Base Assembly

### Sub-assemblies

1 x DIYLB_crank_to_base_assembly | 4 x DIYLB_rail_assembly
DIYLB_crank_to_base_assembled | DIYLB_rail_assembled

### Assembly instructions

DIYLB_columns_to_base_assembly

1. Attach the for columns to the base of the frame
2. Tighten the screws of the L-brackets

DIYLB_columns_to_base_assembled

## DIYLB Bed To Columns Assembly

### Sub-assemblies

2 x DIYLB_carriage_AB_assembly | 1 x DIYLB_columns_to_base_assembly
DIYLB_carriage_AB_assembled | DIYLB_columns_to_base_assembled

### Assembly instructions

DIYLB_bed_to_columns_assembly

1. Thread the assembled carriage holders into the rails and rods of the Z-axis.

DIYLB_bed_to_columns_assembled

## DIYLB Beams To Bed Assembly

### Vitamins

Qty | Description
1 | Flat section 15mmx2mm, 272mm
4 | Flat section 15mmx2mm, 316mm

### 3D Printed parts

8 x DIYLB_beam_holder.stl

DIYLB_beam_holder.stl

### Sub-assemblies

1 x DIYLB_bed_to_columns_assembly

DIYLB_bed_to_columns_assembled

### Assembly instructions

DIYLB_beams_to_bed_assembly

1. Attach the beam holders to the horizontal 20x20 extrusions of the bed.
2. Slide the beams into the beam holders

DIYLB_beams_to_bed_assembled

## DIYLB Top To Columns Assembly

### Sub-assemblies

1 x DIYLB_beams_to_bed_assembly | 2 x DIYLB_top_assembly
DIYLB_beams_to_bed_assembled | DIYLB_top_assembled

### Assembly instructions

DIYLB_top_to_columns_assembly

1. Attach the top extrusions to the rest of the frame.

DIYLB_top_to_columns_assembled

## DIYLB Belt Assembly

### Vitamins

Qty | Description
1 | Belt GT2 x 6mm x 1222mm

### Sub-assemblies

1 x DIYLB_top_to_columns_assembly

DIYLB_top_to_columns_assembled

### Assembly instructions

DIYLB_belt_assembly

1. Insert the timing belt
2. Level the bed by turning the thraded rods, before tightening the pulleys

DIYLB_belt_assembled

Finished!

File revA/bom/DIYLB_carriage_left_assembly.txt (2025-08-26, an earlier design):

DIYLB_carriage_left_assemblies:
Vitamins:
  2 Linear rail carriage MGN7C
  4 Nut M3 x 2.4mm 
  8 Screw M2 cap x 10mm
  4 Screw M3 pan x 16mm
  6 Screw M4 cap x 12mm
  2 T8-Nut (narrow)
  6 T-Nut (20x20)
  8 Washer  M2 x 5mm x 0.3mm
  6 Washer  M4 x 9mm x 0.8mm

Printed:
  2 DIYLB_carriage_left.stl

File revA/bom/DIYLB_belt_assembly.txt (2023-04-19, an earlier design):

DIYLB_belt_assembly:
Vitamins:
  1 Belt GT2 x 6mm x 1104mm

Assemblies:
  1 DIYLB_top_to_columns_assembly

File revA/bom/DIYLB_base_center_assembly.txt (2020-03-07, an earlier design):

DIYLB_base_center_assembly:
Vitamins:
  2 Extrusion E2020 x 320mm
  4 Screw M4 dome x  8mm
  4 T-Nut (20x20)
  4 Washer  M4 x 9mm x 0.8mm

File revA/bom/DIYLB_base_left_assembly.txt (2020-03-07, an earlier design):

DIYLB_base_left_assembly:
Vitamins:
  1 Extrusion E2020 x 300mm
  8 L-Bracket (20x20)
  2 Pulley GT2 idler smooth 12mm
 16 Screw M3 grub x  6mm
  2 Screw M4 cap x 20mm
  2 T-Nut (20x20)
  2 Washer  M4 x 9mm x 0.8mm

Assemblies:
  2 DIYLB_lower_bearing_assemblies

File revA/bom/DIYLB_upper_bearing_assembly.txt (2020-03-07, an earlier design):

DIYLB_upper_bearing_assemblies:
Vitamins:
  4 Ball bearing 608-2RS 8mm x 22mm x 7mm
  4 Screw M3 grub x  4mm
  8 Screw M4 cap x 12mm
  4 Lock ring (8mm)
  8 T-Nut (20x20)
  8 Washer  M4 x 9mm x 0.8mm

Printed:
  4 DIYLB_upper_bearing.stl

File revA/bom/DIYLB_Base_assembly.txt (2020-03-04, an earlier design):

DIYLB_Base_assembly:

Assemblies:
  1 DIYLB_base_center_assembly
  1 DIYLB_base_left_assembly
  1 DIYLB_base_right_assembly

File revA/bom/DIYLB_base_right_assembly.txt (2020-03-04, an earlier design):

DIYLB_base_right_assembly:
Vitamins:
  1 Extrusion E2020 x 300mm
  6 L-Bracket (20x20)
 12 Screw M3 grub x  6mm

Assemblies:
  2 DIYLB_lower_bearing_assemblies

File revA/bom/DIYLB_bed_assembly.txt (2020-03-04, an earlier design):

DIYLB_bed_assembly:
Vitamins:
  4 Extrusion E2020 x 260mm
  2 Extrusion E2020 x 320mm
 12 L-Bracket (20x20)
 24 Screw M3 grub x  6mm

Assemblies:
  2 DIYLB_carriage_left_assemblies
  2 DIYLB_carriage_right_assemblies

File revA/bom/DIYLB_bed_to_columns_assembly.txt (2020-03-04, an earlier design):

DIYLB_bed_to_columns_assembly:

Assemblies:
  1 DIYLB_bed_assembly
  1 DIYLB_columns_to_base_assembly

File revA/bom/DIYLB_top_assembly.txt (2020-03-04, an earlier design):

DIYLB_top_assembly:
Vitamins:
  2 Extrusion E2020 x 300mm

Assemblies:
  4 DIYLB_upper_bearing_assemblies

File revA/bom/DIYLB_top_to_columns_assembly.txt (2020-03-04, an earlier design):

DIYLB_top_to_columns_assembly:

Assemblies:
  1 DIYLB_bed_to_columns_assembly
  1 DIYLB_top_assembly

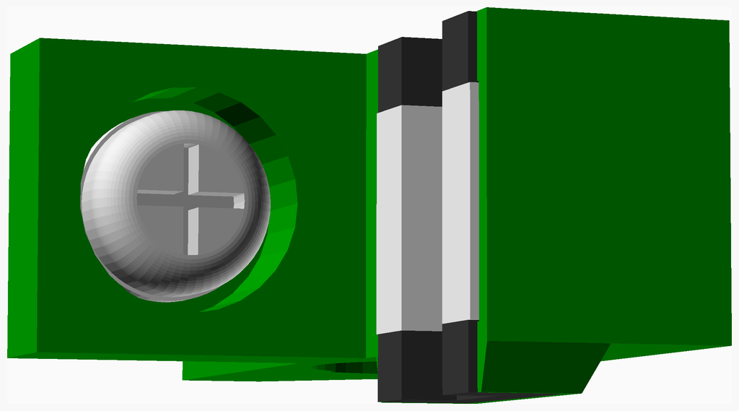
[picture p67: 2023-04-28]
revB/assemblies/DIYLB_carriage_C_assembled.png

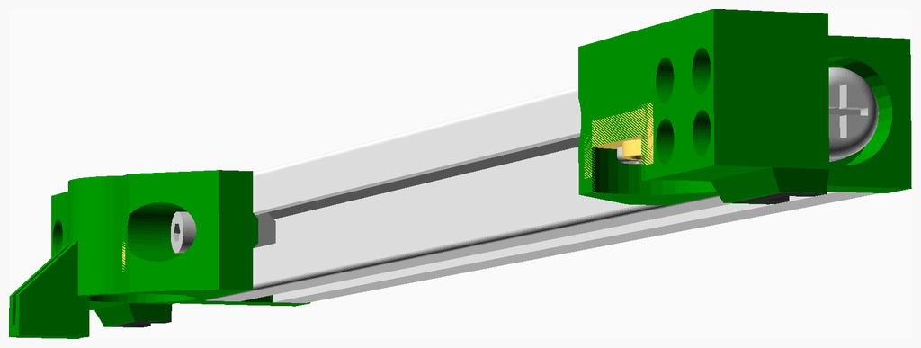
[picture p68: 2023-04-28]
revB/assemblies/DIYLB_carriage_AB_assembly.png

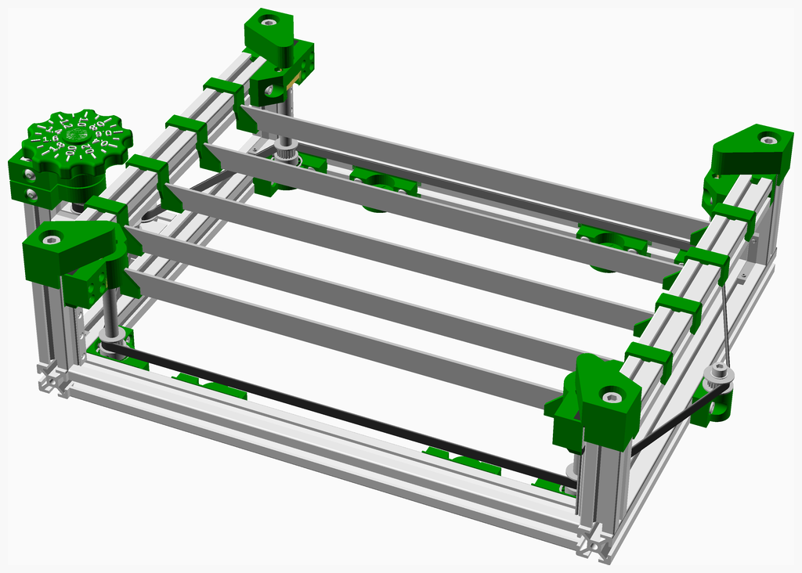
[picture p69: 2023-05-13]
revB/assemblies/DIYLB_belt_assembly.png

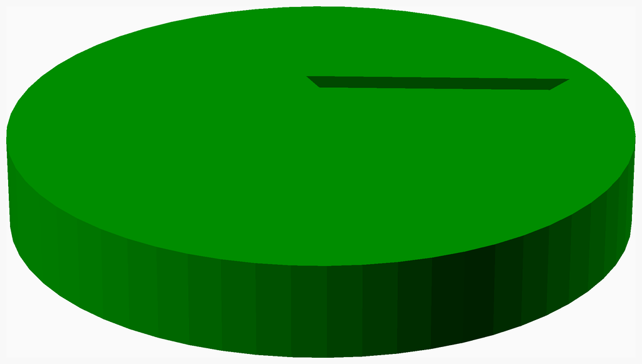
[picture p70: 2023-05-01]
revB/assemblies/DIYLB_magnet_cover_assembly.png

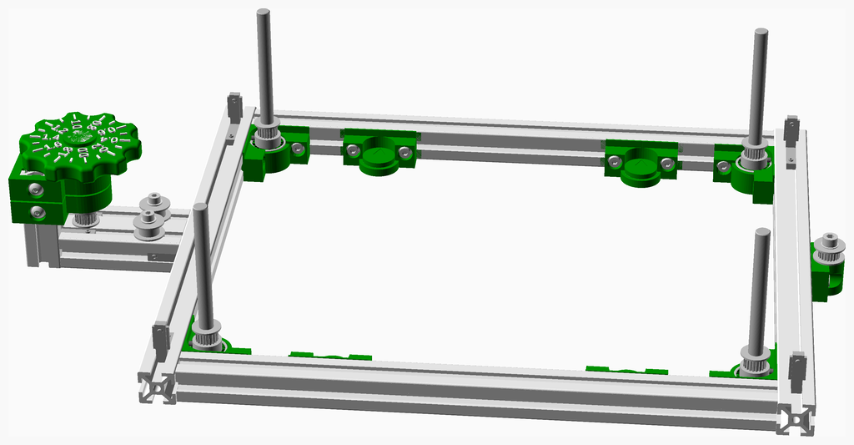
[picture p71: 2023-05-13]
revB/assemblies/DIYLB_crank_to_base_assembled.png

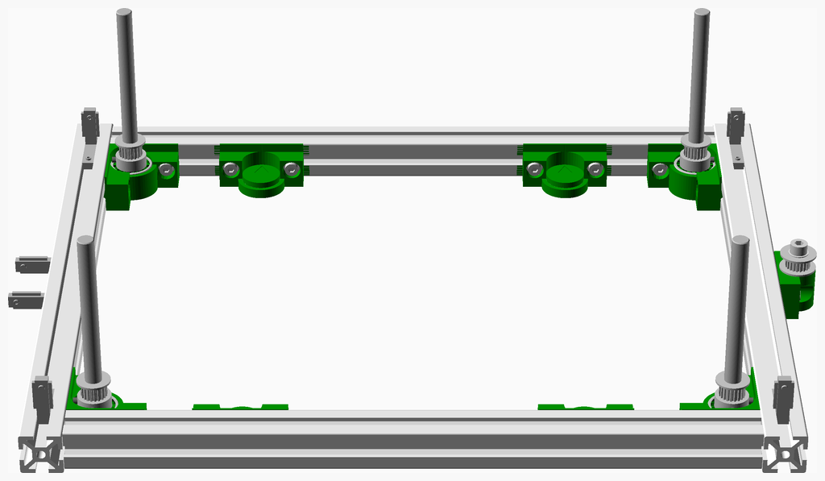
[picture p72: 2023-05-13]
revB/assemblies/DIYLB_Base_assembled.png

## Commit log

2020-02-25 work in progress
    [BB-bracket_old.scad, Cent.scad, Crank.scad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]
2020-02-28 fixed stl and assembly names
    [Cent.scad, Crank.scad, DIYLB.scad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]
2020-02-29 fixes for NopSCADlib update
    [DIYLB_Base.scad, DIYLB_Bed.scad, DIYLB_Carriage.scad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]
2020-03-01 first assembly description
    [DIYLB_CBearing.stl, DIYLB_Carriage.stl, DIYLB_Crank.scad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]
2020-03-02 fixed naming os stls and assemblies
    [DIYLB.scad, DIYLB_Base.scad, DIYLB_Bed.scad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]
2020-03-02 rebuilt instructions
    [DIYLB_carriage_left.stl, DIYLB_carriage_right.stl, DIYLB_crank_bearing.stl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]
2020-03-04 updated instructions
    [DIYLB.scad]
2020-03-07 updated naming and screw lenghts
    [DIYLB_Carriage.scad, DIYLB_LBearing.scad, DIYLB_UBearing.scad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]
2020-03-07 BOM fine tuning
    [DIYLB_Base.scad, DIYLB_Carriage.scad, DIYLB_Crank.scad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]
2020-03-08 updated lower ball bearing holder
    [Cent.scad, DIYLB_Config.scad, DIYLB_LBearing.scad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]
2020-03-10 usung poly_cylinders
    [DIYLB_Carriage.scad, DIYLB_Crank.scad, DIYLB_LBearing.scad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]
2020-03-11 stls with poly_cylinders
    [DIYLB_carriage_left.stl, DIYLB_carriage_right.stl, DIYLB_crank_bearing.stl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]
2020-03-31 fine tuning of printed parts
    [DIYLB_LBearing.scad, DIYLB_UBearing.scad, DIYLB_lower_bearing.stl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]
2020-05-30 removed oversized bearings
    [DIYLB_LBearing.scad, DIYLB_UBearing.scad, DIYLB_lower_bearing.stl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]
2020-05-31 adjtsted carriage stls
    [DIYLB_Carriage.scad, DIYLB_carriage_left.stl, DIYLB_carriage_right.stl]
2020-06-11 design fix
    [DIYLB_Carriage.scad, DIYLB_Rail.scad]
2020-06-11 fixed design flaws
    [DIYLB_Config.scad, DIYLB_Crank.scad, DIYLB_Rail.scad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]
2020-06-11 updated crank wheel
    [DIYLB_Crank.scad, DIYLB_crank.stl]
2020-06-12 redesignes crank wheel
    [DIYLB_Crank.scad]
2020-06-12 updated animated GIF
    [DIYLB_Config.scad]
2023-04-19 minor fix
    [DIYLB_Config.scad]
2023-04-19 moved old design into folder RevA
    [Cent.scad, Crank.scad, DIYLB.scad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]
2023-04-19 moved old design to directory revA
    [Cent.scad, Crank.scad, DIYLB.scad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]
2023-04-19 adapted design for latest NopSCADlib
    [Crank.scad, DIYLB.scad, DIYLB_Bed.scad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]
2023-04-19 fixed animation
    [DIYLB_Config.scad]
2023-04-19 started revB
    [Cent.scad, Crank.scad, DIYLB.scad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]
2023-04-27 revB design finished
    [DIYLB.scad, DIYLB_Base.scad, DIYLB_Bed.scad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]
2023-04-28 NopSCADlib run on revA
    [bom.csv]
2023-04-28 first NopSCADlib run on revB
    [DIYLB.scad, DIYLB_Magnet.scad, DIYLB_beam_holder.stl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]
2023-04-28 switched top readme to revB
2023-04-30 fixed top holders
    [DIYLB_Top.scad, DIYLB_top_A.stl, DIYLB_top_B.stl]
2023-05-01 added magnet cover
    [DIYLB_Magnet.scad, DIYLB_magnet_cover.stl, Magnet.scad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]
2023-05-13 added extra idler
    [DIYLB.scad, DIYLB_AssemblyHelper.scad, DIYLB_Base.scad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]
2023-05-13 added assembly helper
    [DIYLB_AssemblyHelper.stl]
2023-05-14 minor adjustments
    [DIYLB_AssemblyHelper.scad, DIYLB_Idler.scad]
2025-08-26 fixed readme.md
    [DIYLB_AssemblyHelper.stl]
2025-08-26 fixed BOM
    [DIYLB_Carriage.scad, bom.csv]
